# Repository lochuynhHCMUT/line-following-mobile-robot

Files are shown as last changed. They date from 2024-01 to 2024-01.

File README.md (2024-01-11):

# Line following mobile robot with color sensor
This repository contains all files and documents for the Line following mobile robot. The robot was constructed for the Mechatronics Design Project Course at Ho Chi Minh City University of Technology (HCMUT). Our team member includes:
- Huynh Ba Loc
- Phan Dang Khoi Nguyen
- Truong An Quoc
- Nguyen Hoang Minh

The sequence of operation is as follow:
1. Starts following the line until the loading zone, which is marked by a horizontal line.
2. Stops and waits for the package.
3. After the package is loaded, determines its color and chooses a corresponding path.
4. Follows the chosen path.
5. Stops at the end of the line.

The robot can be seen working in [this video](https://youtu.be/HqmgRXV4fzo?si=YYQn4gw1GglHw1m8).



## Building the robot
The robot is built by following [this assembly drawing](ME4071_Mechanical_Assembly_drawing_HuynhBaLoc_NguyenHoangMinh_PhanDangKhoiNguyen_TruongAnQuoc.pdf).

<!-- <img src="3d-robot.png"> -->

## PCB
All required PCBs are located in [this PCB folder](pcb).

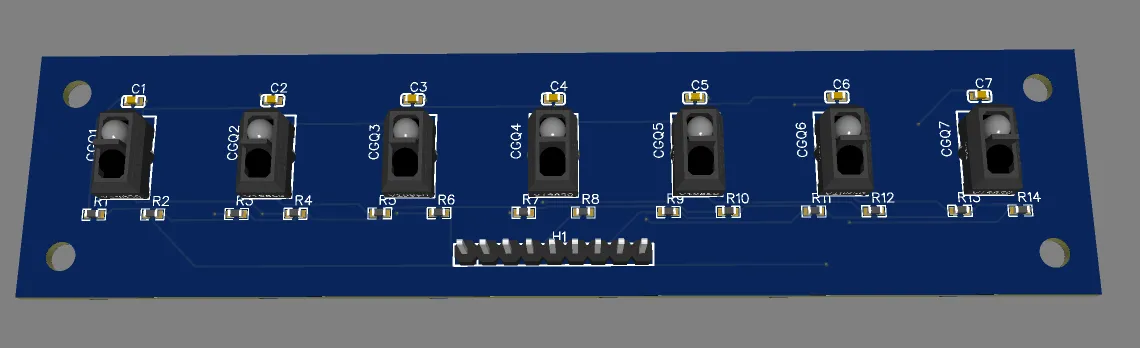
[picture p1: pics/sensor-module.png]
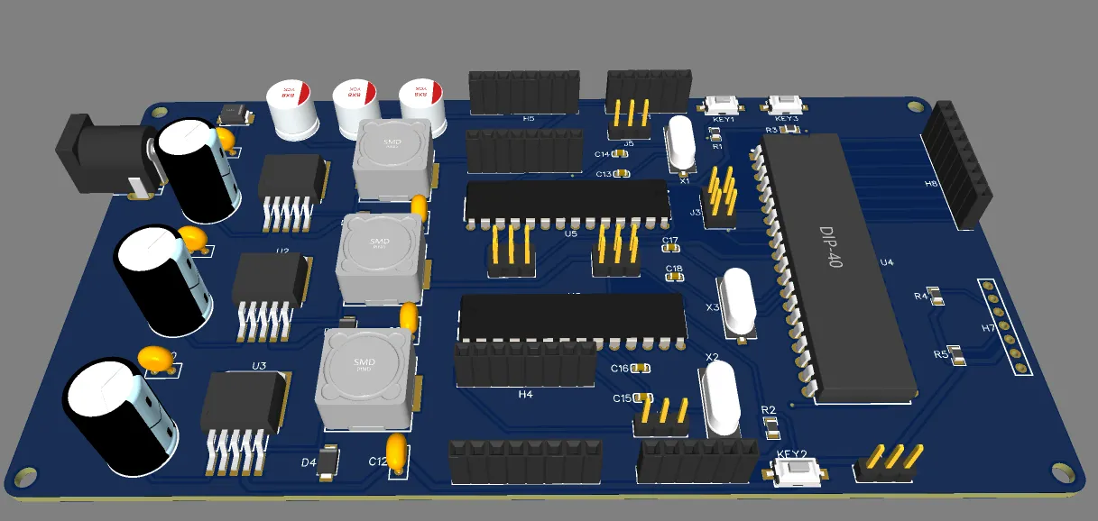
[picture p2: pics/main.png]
 

## Motor PID
To be updated.

## Sensor calibration
After constructing the robot, the line detecting sensor module needs to be calibrated. This MAX-MIN values of each sensor are obtained and set in [the main code](code/A32-MasterMCU.ino).

## Uploading the code
The codes are uploaded using [this AVR USBasp](https://hshop.vn/products/mach-nap-avr-usbasp-2) from Arduino IDE. 

## Notes
To be updated.

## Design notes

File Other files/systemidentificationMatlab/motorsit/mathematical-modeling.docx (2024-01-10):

## 1. Modeling of motor

### 1.1. Define parameters for motor sampling

Test with L298N motor driver

We examine the linear relation between the input (%PWM) and the output revolution of the motor’s shaft (rpm) . To do that, we PWM signal is fed into the motor, duty cycle from 5-100% . After that, we read the rpm signal from the encoder.

Table 4.1. Table of rpm data of motor

%PMW | rpm
5% | 0
10% | 0
15% | 28.133
20% | 50.7385
25% | 69.346
30% | 85.8935
35% | 104.143
40% | 118.375
45% | 129.678
50% | 141.245
55% | 151.046
60% | 161.361
65% | 168.31
70% | 176.172
75% | 181.71
80% | 187.617
85% | 192.982
90% | 198.063
95% | 202.461
100% | 219.046

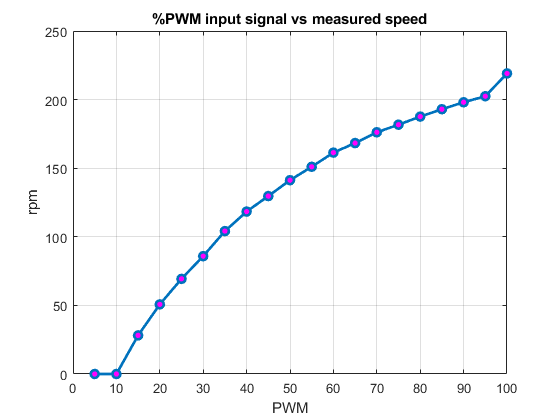
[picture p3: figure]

Fig 4.2. %PWM vs measured velocity (rpm) graph

Test with TB6612 motor driver

Follow the same procedure as above:

Table 4.2. Table of rpm data of motor

%PMW | rpm
5% | 0
10% | 21.4281
15% | 33.0784
20% | 45.6978
25% | 59.2714
30% | 71.612
35% | 85.1655
40% | 98.9197
45% | 111.3331
50% | 123.494
55% | 136.1053
60% | 149.1838
65% | 162.2477
70% | 176.4101
75% | 187.6647
80% | 198.401
85% | 214.4792
90% | 229.4622
95% | 241.7738
100% | 254.8411

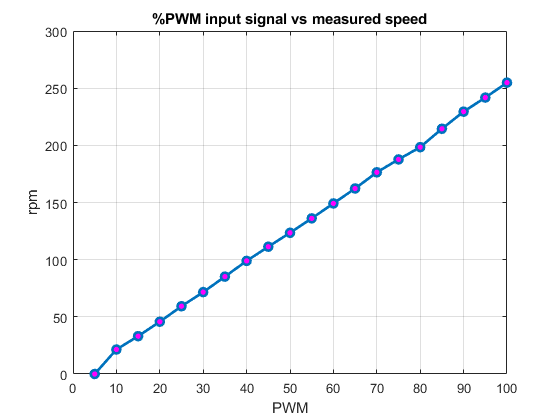
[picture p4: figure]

Fig 4.3. %PWM vs measured velocity (rpm) graph

We see that the TB6612 helps making the relationship between PWM and speed linear better than L298N.

### 1.2. Determine motor transfer function

Prepare data for SIT

Let a PWM input changes in the function f(t)=127.5sin(t)+127.5

→T=6.28(s)

Then:

N×δt=m×T

δt is from the Nyquist criterion

f_(Sampling) ≥2f_(signal) →δt≤1/2T

Our T satisfy the condition.

→N×0.022=m×6.2832

We choose N=1428; m=5 (must be integer)

For the motor, the output signal is the revolution of the output shaft (rpm) , input is PWM in a sinusoidal wave. So in order to obtain the motor transfer function, we will provide the motor with %PWM , then measure the revolution of the output shaft.

- Plotting the input and output data. We obtain the following graph:

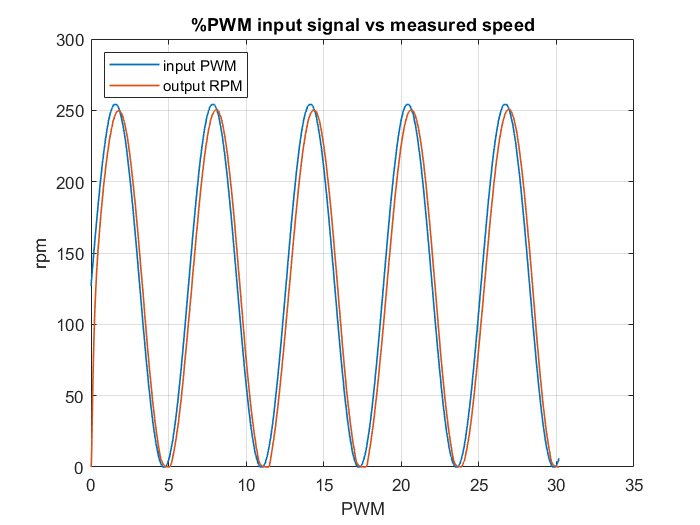
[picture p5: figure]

Fig 4.3. Measured speed of the motor

- Using MATLAB System Identification Toolbox (SIT), we yield the following transfer function of the motor-driver plant 1

G(s)=1.008/(0.18162×s+1)= 5.55/(s+5.51)

| Current value
Settling time | T_s =0.18162×4=0.72648 (s)
Overshoot | 1%
Steady-state error for step input | 0.01

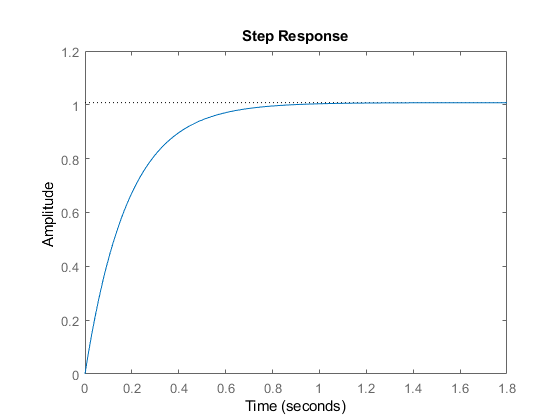
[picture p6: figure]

Fig 4.4. Step response graph of the transfer function

We want to make the motor-driver settling time smaller than the sampling time of the microcontroller so that it can work fine. T_s <δt

Select T_s =0.015 s

Keep the overshoot at this moment. We also want to remove steady-state error for step input

With the above requirements, we implement the PI controller for this motor-driver plant. Assuming negative unity feedback, the forward transfer function will be

K((s+a_2 ))/s×5.55/(s+5.51)

ζ=-(ln(%OS))/(√(ln(%OS)^2 +π^2))=-(ln(0.01))/(√(ln(0.01)^2 +π^2))=0.8261

T_s =0.015=(-ln(0.02√(1-ζ^2)))/(ζω_n)→ω_n =(-ln(0.02√(1-0.8261^2)))/(0.015×0.8261)=361.991

Then the PI controller:

(K(s+a_2 ))/s

Desired characteristics equation for negative unity feedback:

1+(K(s+a_2 ))/s5.55/(s+5.51)=0→s^2 +5.51s+5.55Ks+5.55Ka_2 =0→{, ω_n =√(5.55Ka_2)=361.991, ζ=(5.51+5.55K)/(2ω_n)=(5.51+5.55K)/(2×361.991)=0.8261→{, a_2 =(361.991^2)/(106.7696×5.55)=221.1336, K=106.7696

The open loop TF:

(106.7696(s+221.1336))/s×5.55/(s_0 +5.51)

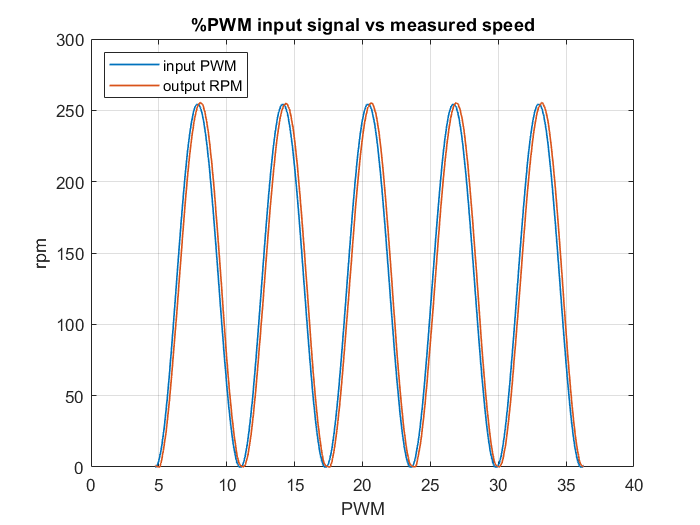
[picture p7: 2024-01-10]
Other files/systemidentificationMatlab/motorsit/motor2data.png

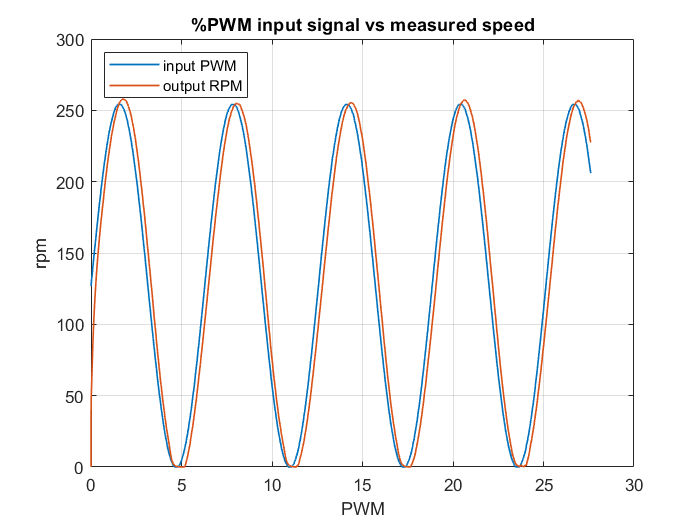
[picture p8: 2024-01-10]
Other files/systemidentificationMatlab/motorsit/checklinear(GM25+TB6612)/plotbytime.png

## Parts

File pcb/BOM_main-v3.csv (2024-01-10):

ID | Name | Designator | Footprint | Quantity
1 | 680uF | C1,C5,C9 | CAP-TH_BD10.0-P5.00-D1.0-FD | 3
2 | 100nF | C2,C4,C6,C8,C10,C12 | CAP-TH_L5.0-W2.5-P2.54-D0.7 | 6
3 | 220uF | C3,C7,C11 | CAP-TH_BD8.0-P3.50-D0.6-FD | 3
4 | 22p | C13,C14,C15,C16,C17,C18 | C0603 | 6
5 | SS34-SMB | D1,D5 | SMB_L4.4-W3.6-LS5.3-RD | 2
6 | IN5824 | D2,D3,D4 | SMAF_L3.5-W2.6-LS4.7-RD | 3
7 | DC005-2.0MM | DC1,DC2 | DC-IN-TH_DC005 | 2
8 | GM25 | H1,H2 | HDR-F-2.54_1X6 | 2
9 | TB6612 BLeft | H3 | HDR-F-2.54_1X8 | 1
10 | TB6612 BRight | H4 | HDR-F-2.54_1X8 | 1
11 | TB6612 ALeft | H5 | HDR-F-2.54_1X8 | 1
12 | TB6612 ARight | H6 | HDR-F-2.54_1X8 | 1
13 | TCS34725 | H7 | FEMALE-HEADER-1X7 | 1
14 | TCRT5000 MODULE | H8 | HDR-F-2.54_1X9 | 1
15 | ICSP_SlaveA | J1 | HDR-M-2.54_2X3 | 1
16 | ICSP_SlaveB | J2 | HDR-M-2.54_2X3 | 1
17 | ICSP_Master | J3 | HDR-M-2.54_2X3 | 1
18 | UART_Master | J4 | HDR-M-2.54_1X4 | 1
19 | UART_SlaveA | J5 | HDR-M-2.54_1X3 | 1
20 | UART_SlaveB | J6 | HDR-M-2.54_1X3 | 1
21 | K2-3.6×6.1_SMD | KEY1,KEY2,KEY3 | KEY-SMD_2P-L6.2-W3.6-LS8.0 | 3
22 | 33uH | L1,L2,L3 | IND-SMD_L12.3-W12.3 | 3
23 | 10k | R1,R2,R3 | R0805 | 3
24 | 1k | R4,R5 | R0805 | 2
25 | LM2596S-12 | U1 | TO-263-5_L10.1-W8.7-P1.70-LS15.2-BR | 1
26 | LM2596S-5 | U2 | TO-263-5_L10.1-W8.7-P1.70-LS15.2-BR | 1
27 | LM2596S-3.3 | U3 | TO-263-5_L10.1-W8.7-P1.70-LS15.2-BR | 1
28 | ATMEGA32A-PU_Master | U4 | DIP-40_L52.3-W13.9-P2.54-LS15.2-BL | 1
29 | ATMEGA328P-PU_SlaveA | U5 | DIP-28_L34.6-W7.3-P2.54-LS10.2-BL | 1
30 | ATMEGA328P-PU_SlaveB | U6 | DIP-28_L34.6-W7.3-P2.54-LS10.2-BL | 1
31 | 16MHz | X1,X2,X3 | CRYSTAL-SMD_L11.4-W4.5-LS12.5 | 3

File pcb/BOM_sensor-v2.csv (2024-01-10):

ID | Name | Designator | Footprint | Quantity
1 | 100nF | C1,C2,C3,C4,C5,C6,C7 | CAP-TH_L5.0-W2.5-P2.54-D0.7 | 7
2 | TCRT5000L | CGQ1,CGQ2,CGQ3,CGQ4,CGQ5,CGQ6,CGQ7 | OPTO-TH_TCRT5000L | 7
3 | HDR-M-2.54_1x9 | J1 | HDR-M-2.54_1X9 | 1
4 | 4k7 | R1,R3,R5,R7,R9,R11,R13 | R0603 | 7
5 | 220 | R2,R4,R6,R8,R10,R12,R14 | R0603 | 7

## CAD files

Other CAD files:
File CAD 2023/Assembly drawing.dwg
File CAD 2023/Selection and Algorithms.dwg
File CAD 2023/Electrical drawing.dwg

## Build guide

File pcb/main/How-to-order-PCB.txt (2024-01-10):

How to Order PCB

Please refer to:
https://docs.easyeda.com/en/PCB/Order-PCB

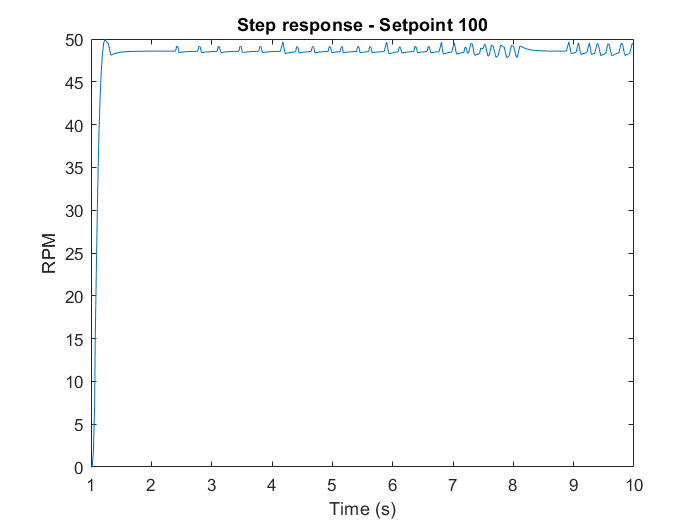
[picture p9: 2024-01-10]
Other files/systemidentificationMatlab/motorsit/step100.png

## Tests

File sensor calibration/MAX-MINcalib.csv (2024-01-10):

 | CB1 | CB2 | CB3 | CB4 | CB5 | CB6 | CB7
 | 467 | 48 | 48 | 39 | 39 | 37 | 39
 | 468 | 52 | 37 | 39 | 39 | 37 | 40
 | 468 | 45 | 37 | 39 | 40 | 32 | 26
 | 469 | 41 | 40 | 40 | 26 | 26 | 30
 | 468 | 45 | 37 | 39 | 39 | 33 | 40
 | 466 | 48 | 48 | 48 | 39 | 37 | 39
 | 450 | 34 | 34 | 38 | 48 | 48 | 39
 | 464 | 52 | 37 | 39 | 39 | 37 | 40
 | 465 | 41 | 40 | 26 | 26 | 30 | 35
 | 463 | 40 | 40 | 26 | 27 | 31 | 38
 | 464 | 48 | 48 | 39 | 39 | 37 | 39
 | 465 | 40 | 26 | 26 | 30 | 34 | 38
 | 451 | 26 | 27 | 34 | 38 | 48 | 48
 | 468 | 45 | 37 | 39 | 40 | 32 | 26
 | 458 | 39 | 48 | 48 | 48 | 37 | 39
 | 458 | 40 | 26 | 30 | 34 | 38 | 48
 | 468 | 45 | 41 | 40 | 26 | 26 | 30
 | 464 | 52 | 39 | 39 | 39 | 41 | 40
 | 458 | 42 | 48 | 48 | 39 | 37 | 39
 | 446 | 30 | 30 | 38 | 38 | 48 | 48
 | 456 | 40 | 26 | 30 | 34 | 38 | 48
 | 463 | 40 | 26 | 26 | 30 | 34 | 38
 | 464 | 52 | 39 | 39 | 39 | 37 | 40
 | 446 | 30 | 30 | 38 | 38 | 48 | 48
 | 446 | 30 | 31 | 38 | 38 | 48 | 48
 | 447 | 30 | 31 | 38 | 48 | 48 | 48
 | 468 | 45 | 39 | 40 | 40 | 26 | 27
 | 466 | 48 | 48 | 39 | 39 | 37 | 39
 | 466 | 45 | 39 | 39 | 39 | 33 | 40
 | 469 | 45 | 41 | 40 | 26 | 26 | 30
 | 463 | 40 | 26 | 30 | 34 | 35 | 48
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

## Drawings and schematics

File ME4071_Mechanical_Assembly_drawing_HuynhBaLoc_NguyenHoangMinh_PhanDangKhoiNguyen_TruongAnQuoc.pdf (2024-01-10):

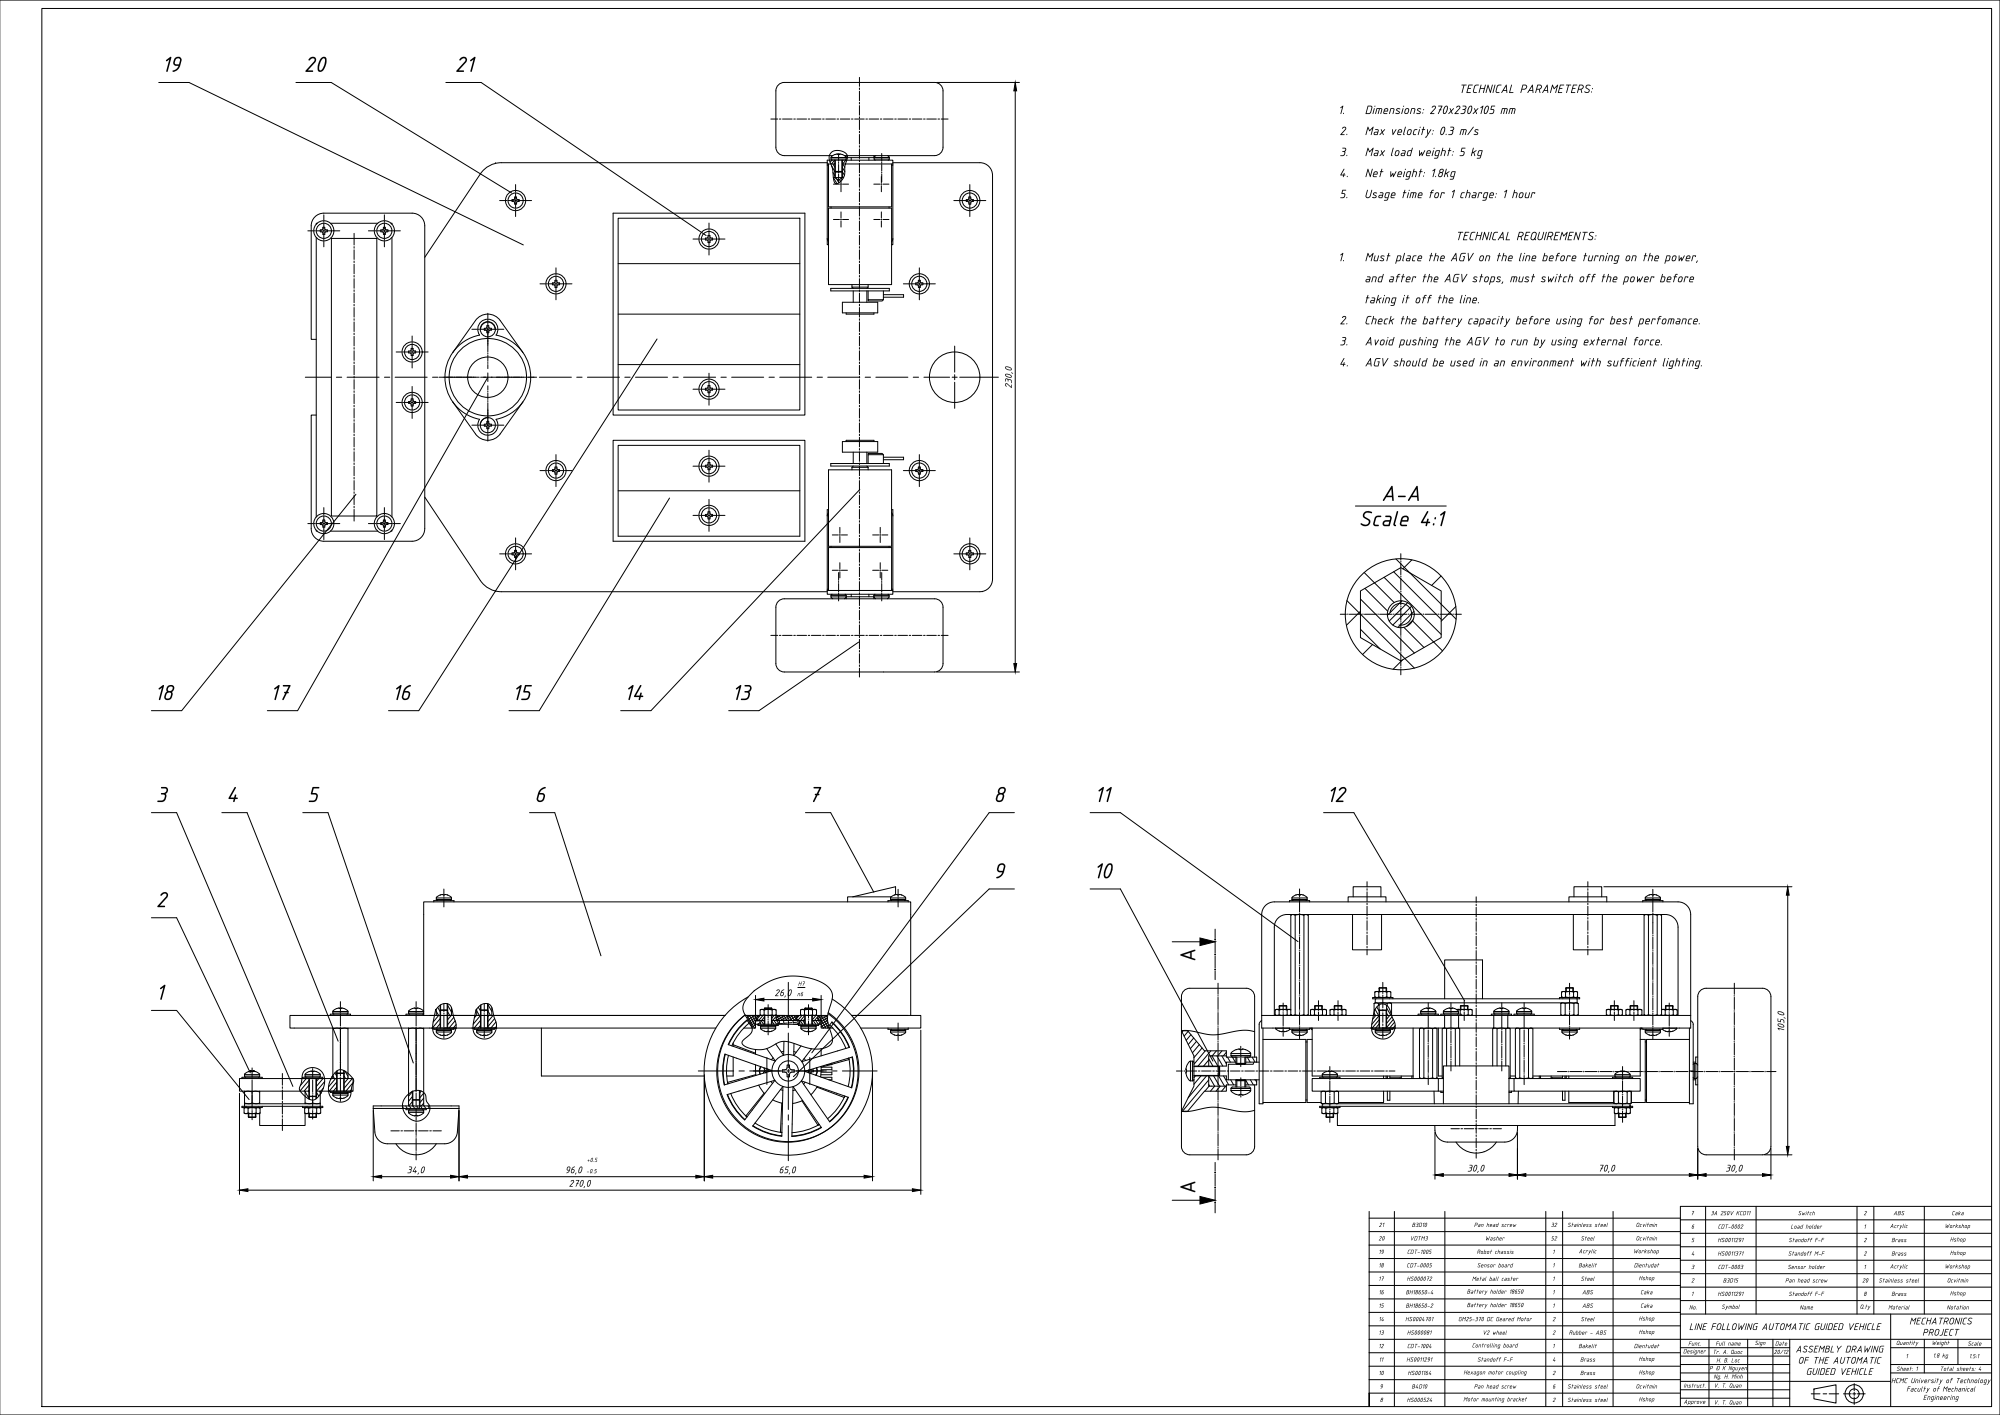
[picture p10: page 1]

230,0 Func. Full name Sign Date Quantity Weight Scale 1 Sheet: 1 Total sheets: 4 Designer Instruct. Approve Tr. A. Quoc V. T. Quan V. T. Quan 20/12 MECHATRONICS PROJECT ASSEMBLY DRAWING OF THE AUTOMATIC GUIDED VEHICLE LINE FOLLOWING AUTOMATIC GUIDED VEHICLE HCMC University of Technology Faculty of Mechanical Engineering 1.8 kg 1.5:1 H. B. Loc P Đ K Nguyen Ng. H. Minh No. Symbol Name Q.ty Material Notation 1 Standoff F-F 8 Brass 2 Pan head screw 20 Stainless steel 3 Sensor holder 1 Acrylic 4 Standoff M-F 2 Brass 5 HS0011291 HS0011371 HS0011291 Standoff F-F 2 Brass 6 Load holder 1 Acrylic 8 Motor mounting bracket 2 Stainless steel 10 Controlling board 1 Bakelit 11 V2 wheel 2 12 Battery holder 18650 1 ABS 131415 Metal ball caster 1 16 Sensor board 1 17 Steel HS000524 HS000081 Battery holder 18650 1 ABS HS0004701 GM25-370 DC Geared Motor 2 Bakelit HS000072 HS0011291 Standoff F-F 4 Brass 1819 Robot chassis 1 Acrylic HS001164 Hexagon motor coupling 2 Brass 20 Washer 52 Steel 9 Pan head screw 6 Stainless steel 21 Pan head screw 32 Stainless steel 7 3A 250V KCD11 Switch 2 A-A Scale 4:1 TECHNICAL PARAMETERS: 1. Dimensions: 270x230x105 mm 2. Max velocity: 0.3 m/s 3. Max load weight: 5 kg 4. Net weight: 1.8kg 5. Usage time for 1 charge: 1 hour TECHNICAL REQUIREMENTS: 1. Must place the AGV on the line before turning on the power, and after the AGV stops, must switch off the power before taking it off the line. 2. Check the battery capacity before using for best perfomance. 3. Avoid pushing the AGV to run by using external force. 4. AGV should be used in an environment with sufficient lighting. B3D15 CDT-0003 CDT-0002 CDT-1005 CDT-1004 CDT-0005 B4D10 VDTM3 B3D10 BH18650-2 BH18650-4 Steel Rubber - ABS ABS Hshop Hshop Hshop Hshop Hshop Hshop Hshop Hshop Hshop Ocvitmin Ocvitmin Ocvitmin Ocvitmin Workshop Workshop Workshop Caka Caka Caka Dientudat Dientudat 30,0 70,0 30,0 H7 26,0 n6

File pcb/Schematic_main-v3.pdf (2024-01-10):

# C18 ¹⁶MHz X³

# C16 ¹⁶MHz X²

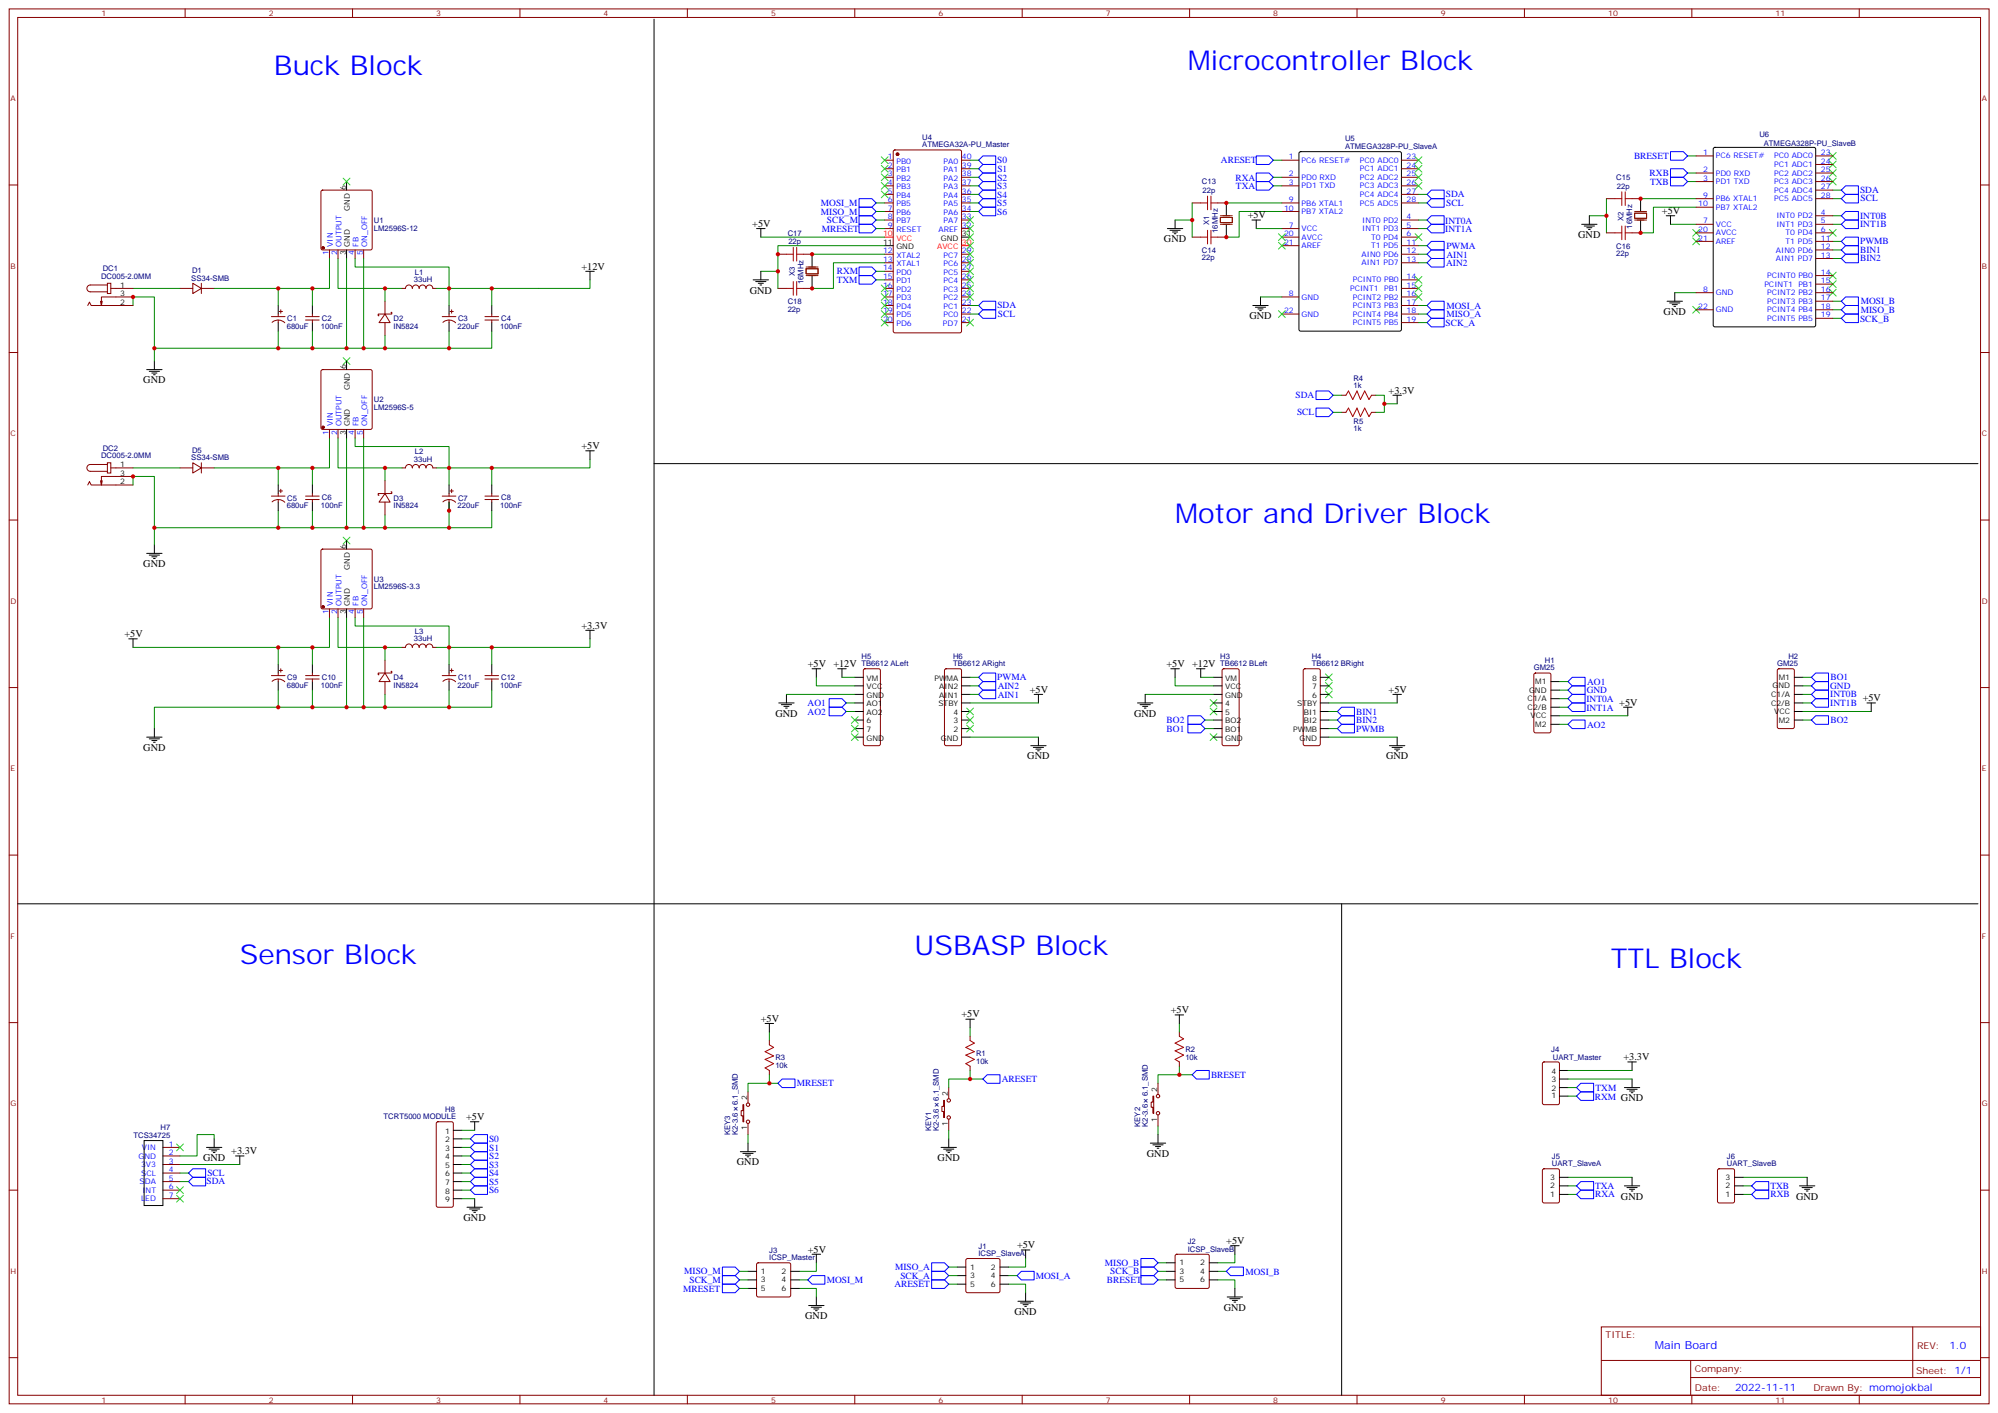
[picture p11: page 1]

Motor and Driver Block

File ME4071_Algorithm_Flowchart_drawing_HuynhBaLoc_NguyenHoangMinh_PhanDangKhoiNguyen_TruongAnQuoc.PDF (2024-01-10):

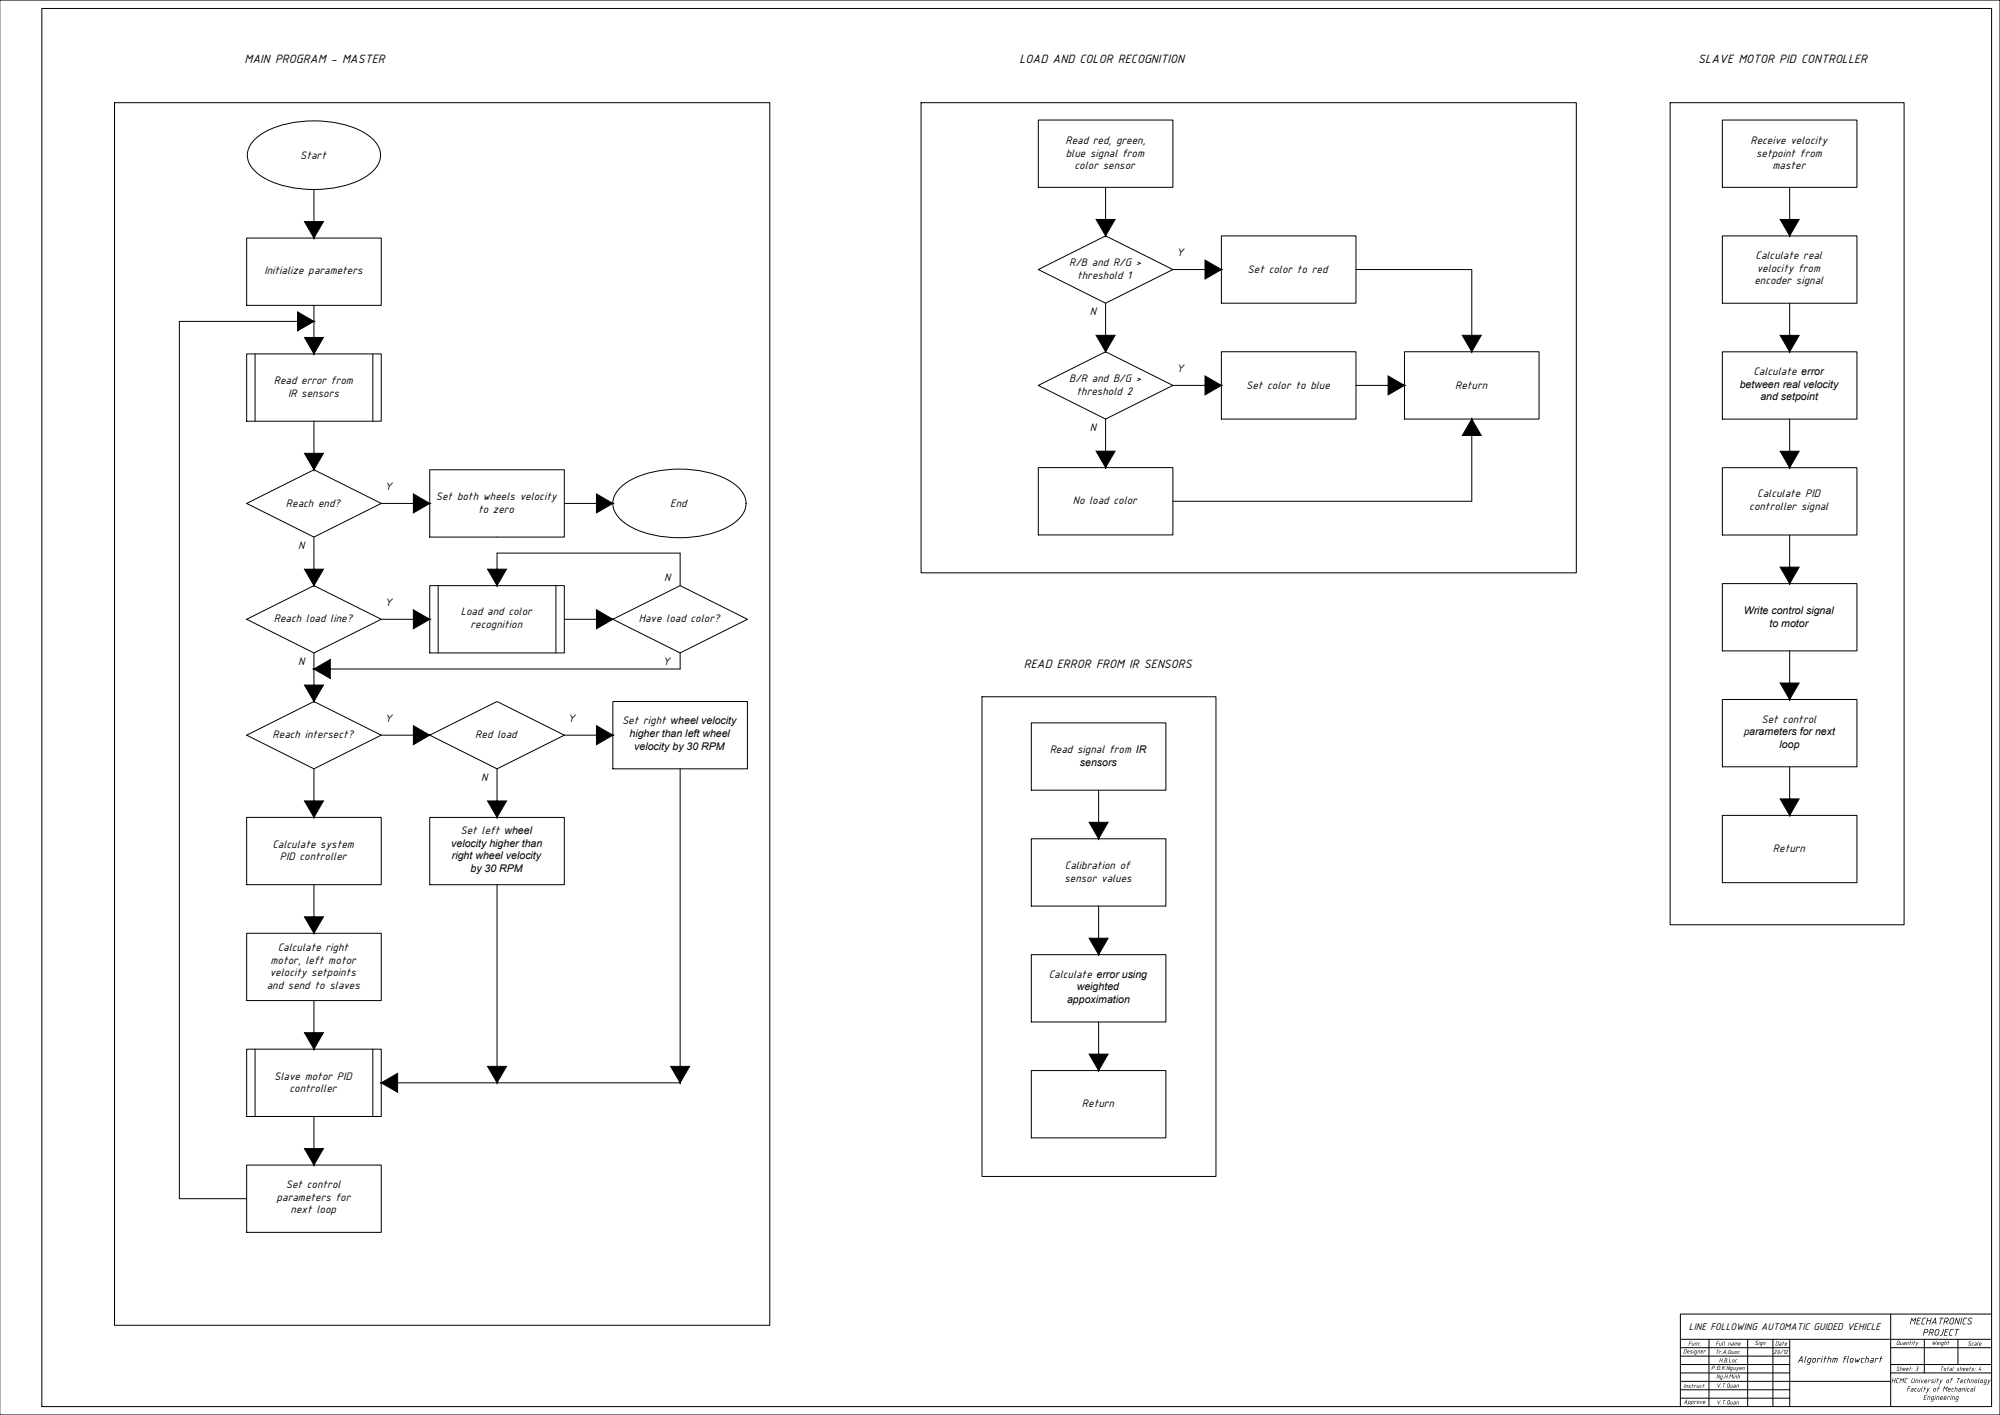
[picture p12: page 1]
MAIN PROGRAM - MASTER; LOAD AND COLOR RECOGNITION; SLAVE MOTOR PID CONTROLLER READ ERROR FROM IR SENSORS Start Initialize parameters Read error from IR sensors Reach end?; Set both wheels velocity to zero; End N Reach load line?; Load and color recognition N Reach intersect?; Red load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

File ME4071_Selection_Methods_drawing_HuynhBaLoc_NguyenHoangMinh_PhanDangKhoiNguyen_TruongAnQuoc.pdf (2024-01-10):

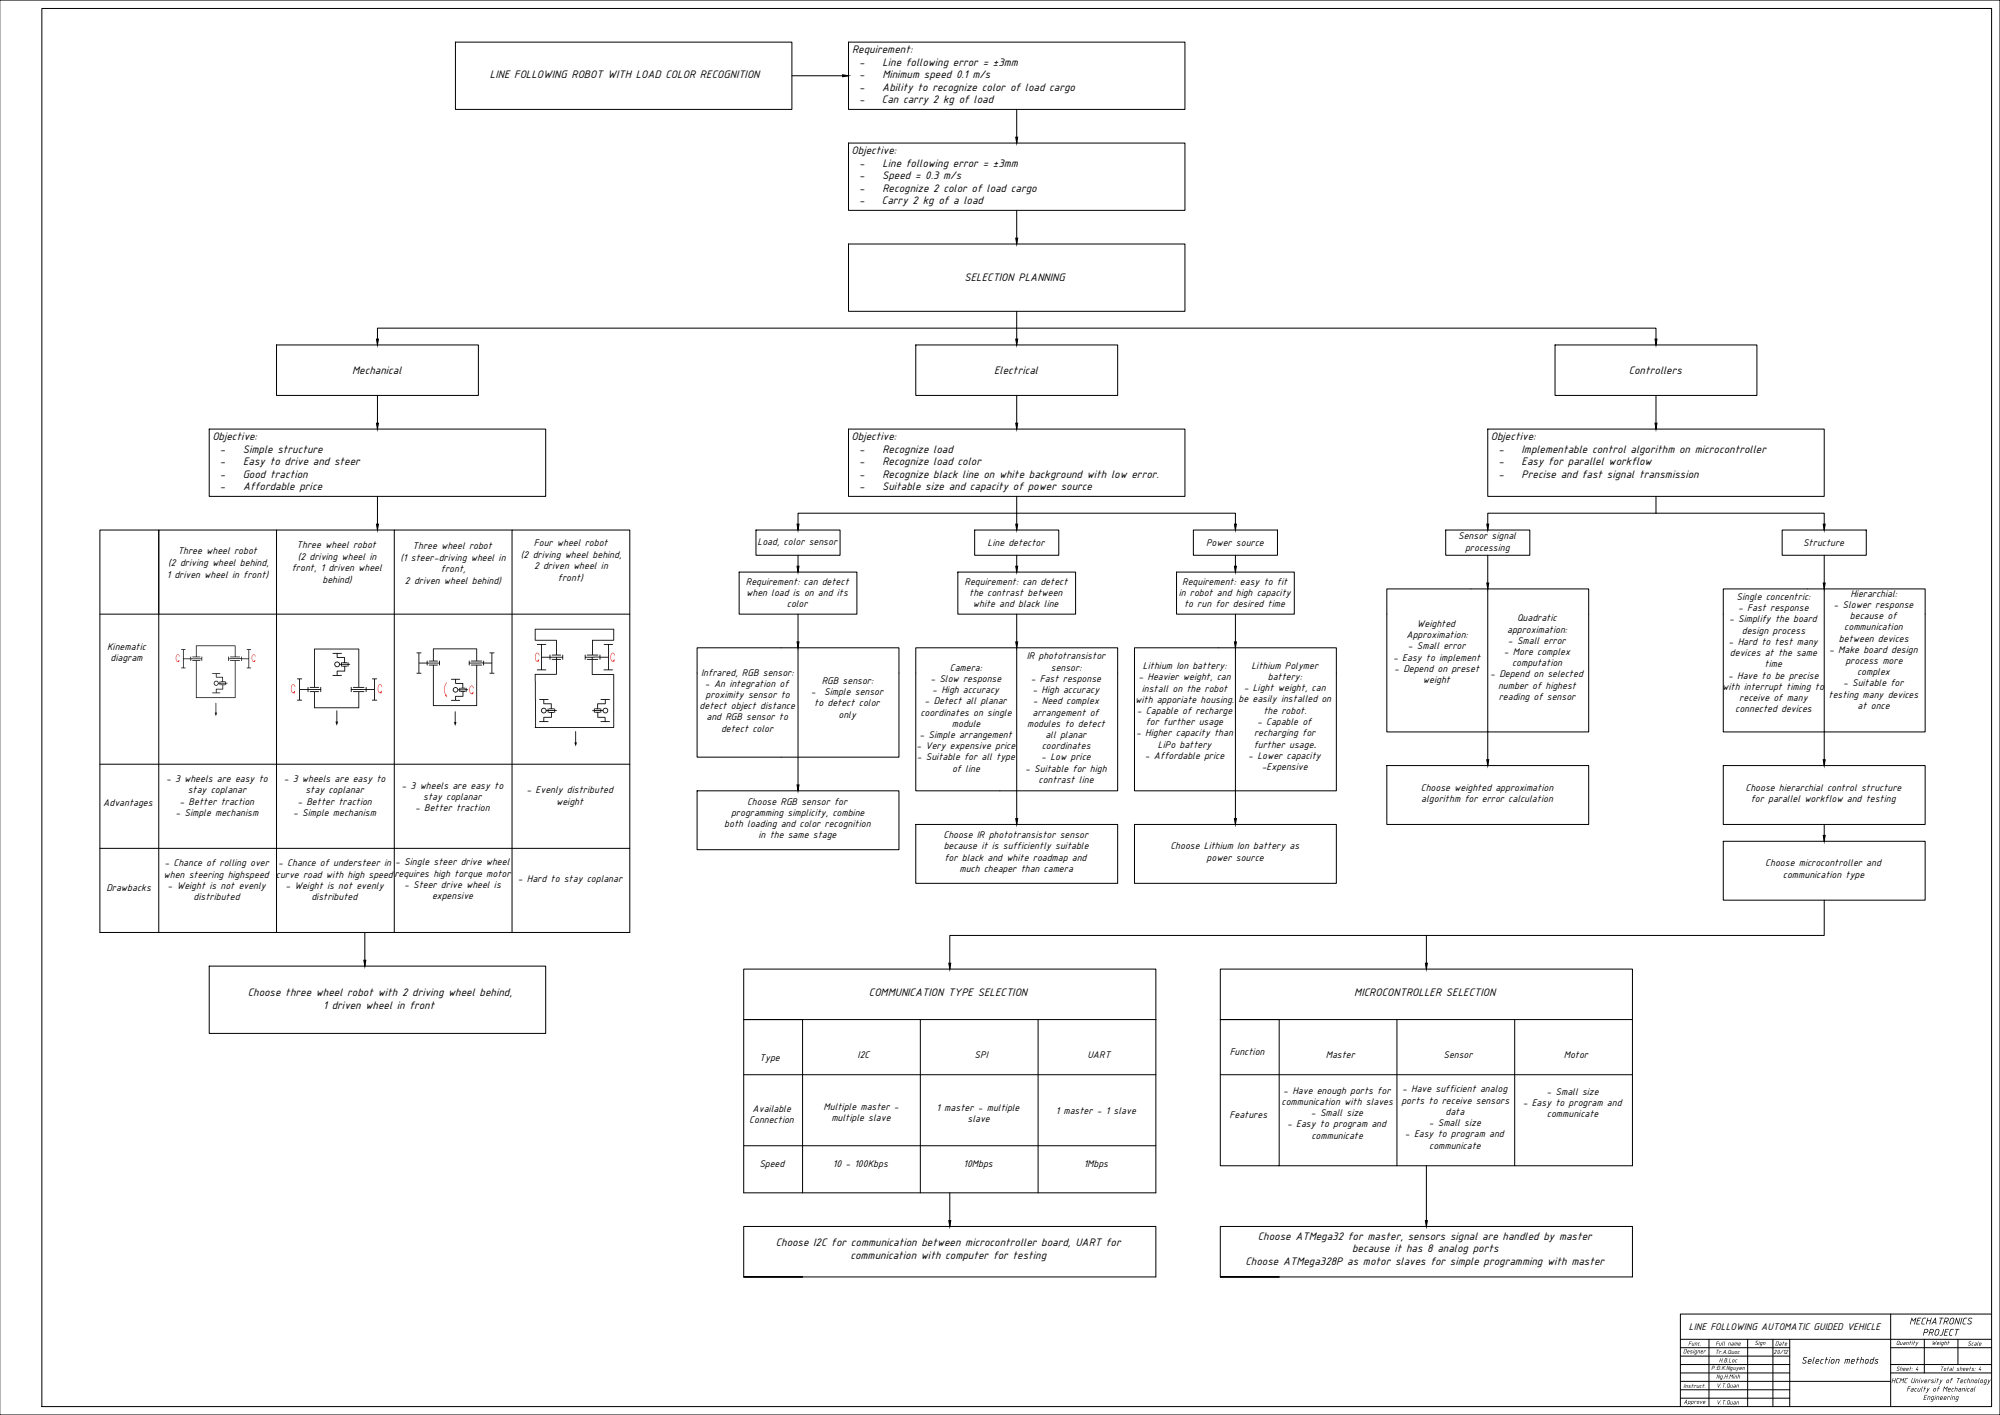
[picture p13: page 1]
Three wheel robot (2 driving wheel behind, 1 driven wheel in front); Three wheel robot (2 driving wheel in front, 1 driven wheel behind); Four wheel robot (2 driving wheel behind, 2 driven wheel in front) Three wheel robot (1 steer-driving wheel in front, 2 driven wheel behind); Load, color sensor; Line detector; Power source; Sensor signal processing; Structure Kinematic diagram Advantages Drawbacks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

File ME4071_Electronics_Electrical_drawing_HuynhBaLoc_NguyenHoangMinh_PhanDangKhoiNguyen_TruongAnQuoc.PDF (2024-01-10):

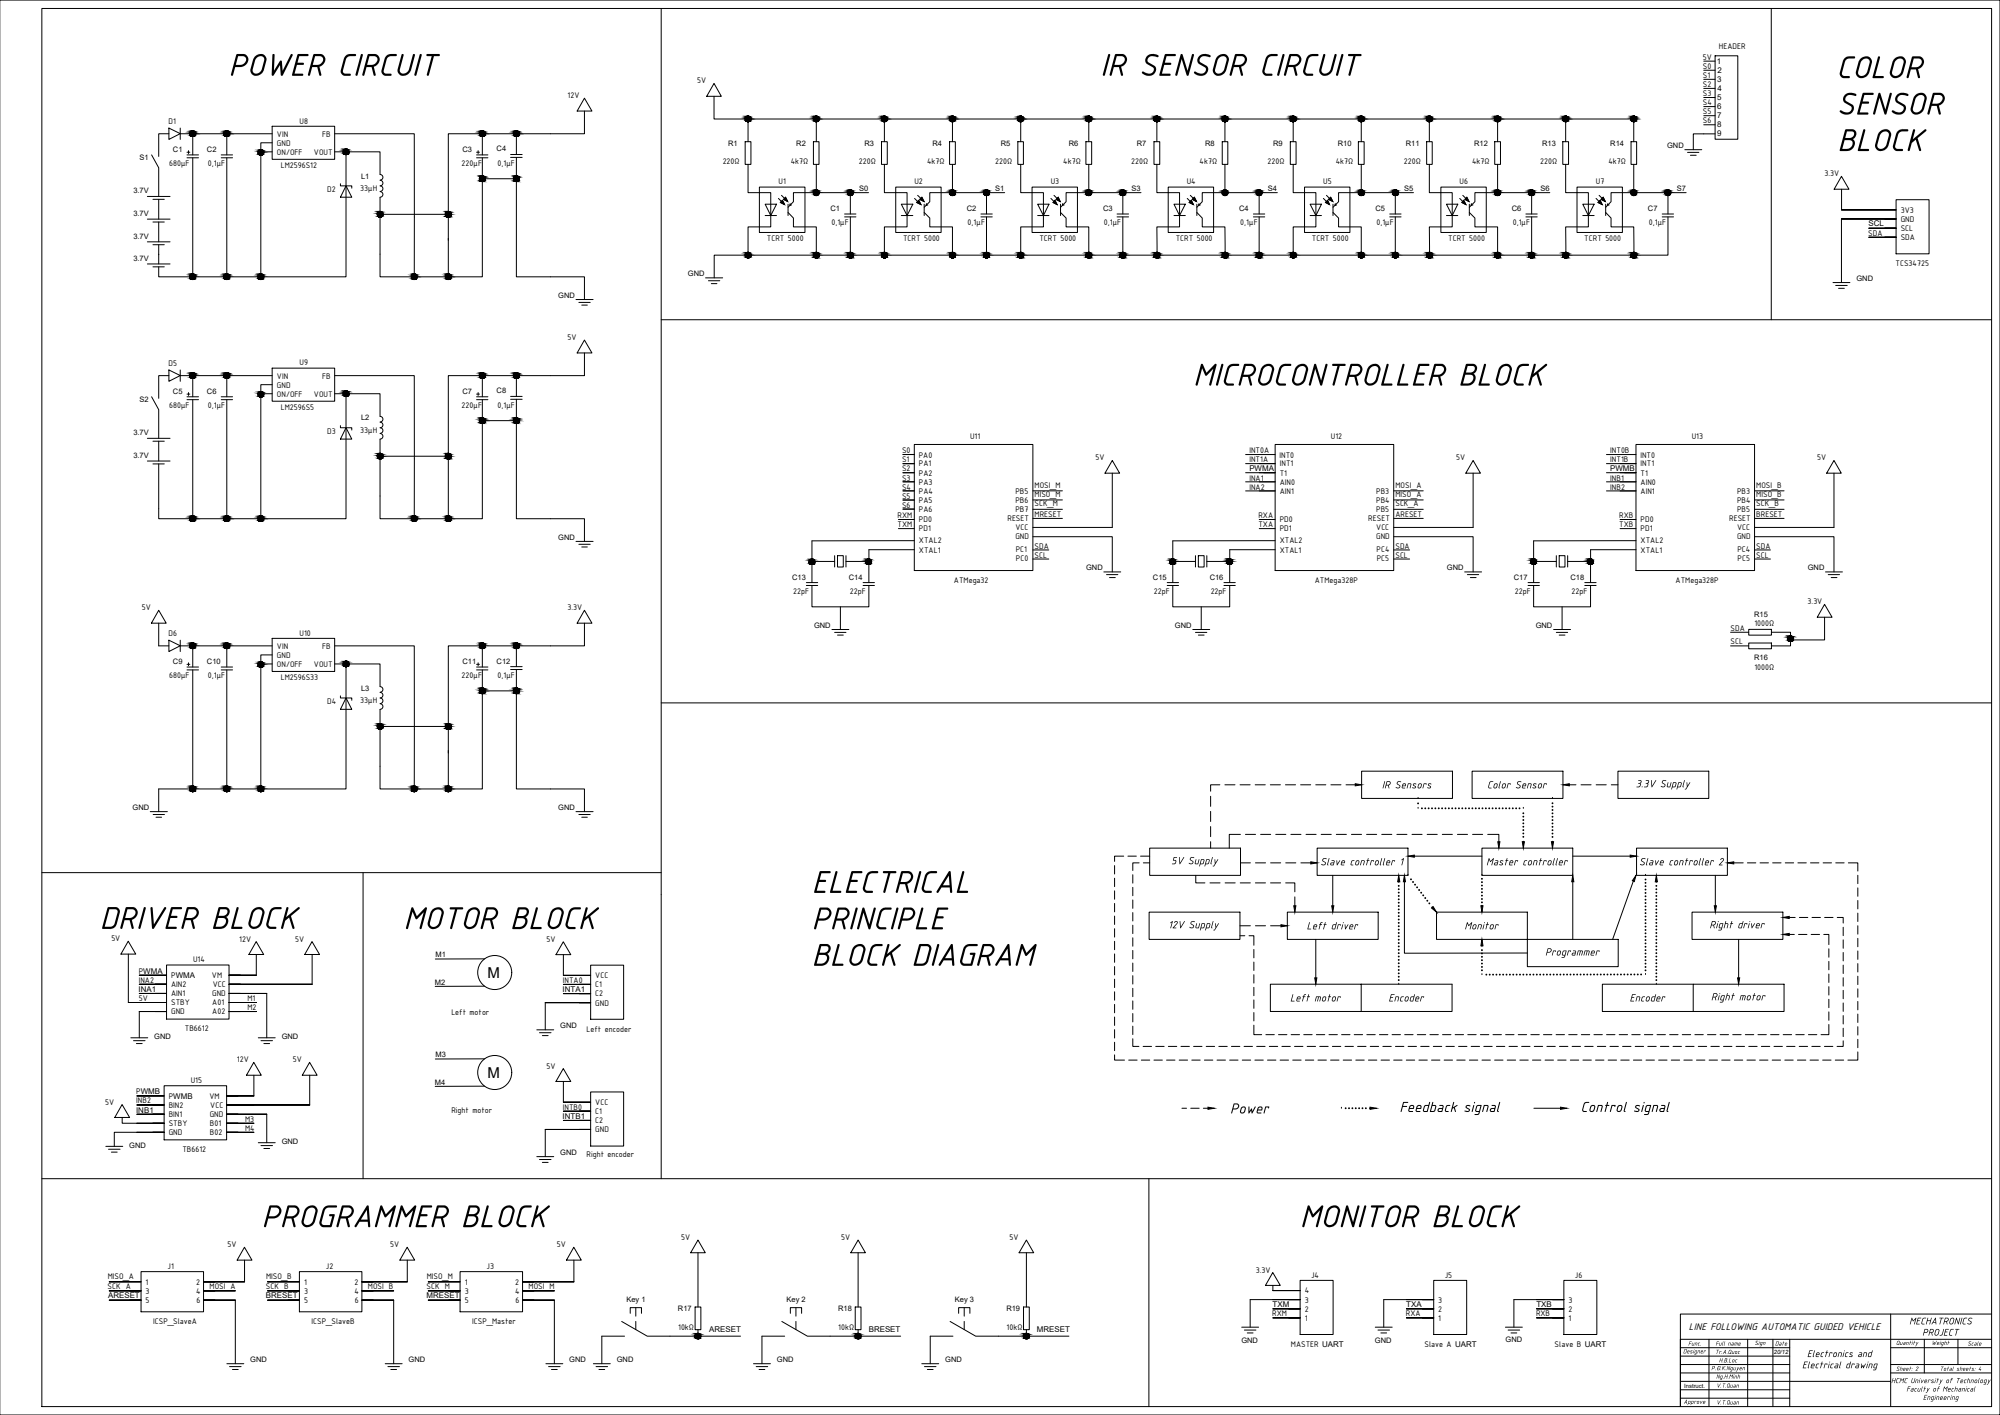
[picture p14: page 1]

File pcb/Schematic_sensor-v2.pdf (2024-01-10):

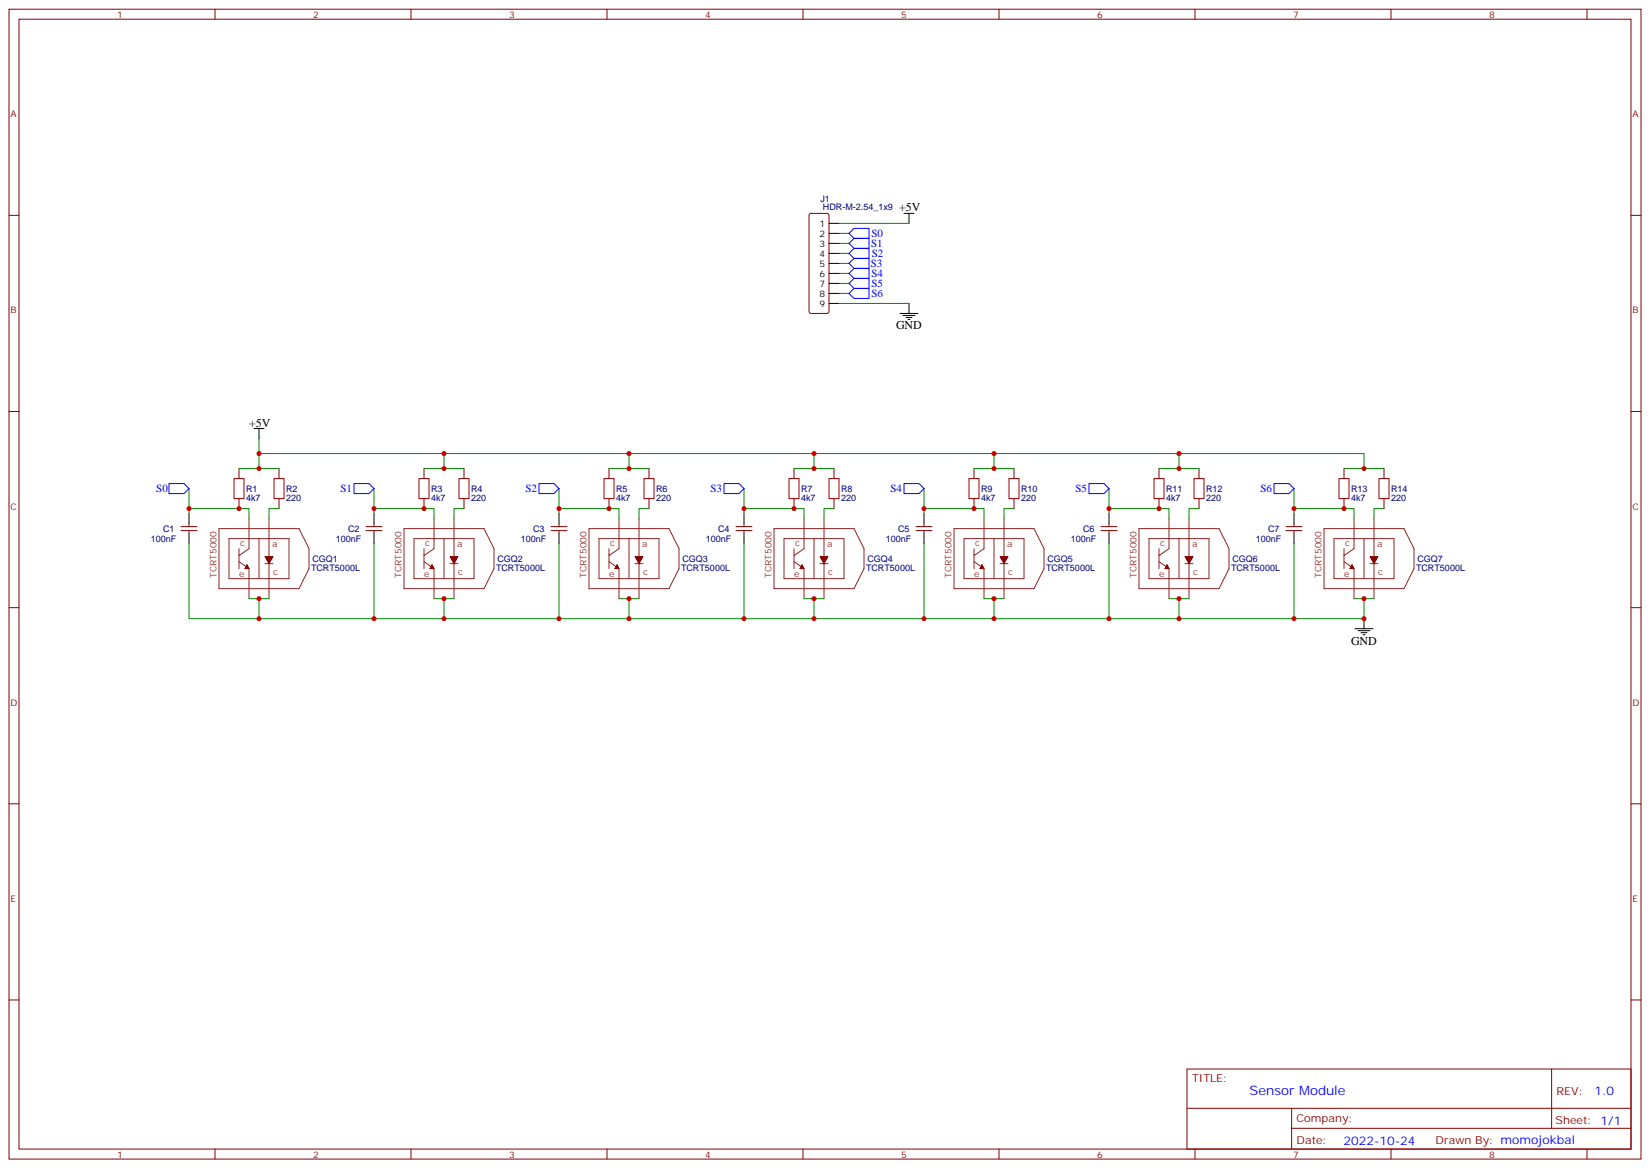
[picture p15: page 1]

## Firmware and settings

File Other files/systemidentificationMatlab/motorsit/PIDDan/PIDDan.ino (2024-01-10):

// Pins
#define ENCA 2
#define ENCB 3
#define PWM 5
#define IN1 7
#define IN2 6

// globals
long prevT = 0;
int posPrev = 0;
// Use the "volatile" directive for variables
// used in an interrupt
volatile int pos_i = 0;
volatile float velocity_i = 0;
volatile long prevT_i = 0;

float v1Filt = 0;
float v1Prev = 0;
float eprop =0, eder = 0, ePrev =0, ePast = 0;
float eintegral = 0;
float uPrev = 0;
int pwr = 120;
float vt = 120;
void setup() {
  Serial.begin(9600);
  pinMode(ENCA,INPUT);
  pinMode(ENCB,INPUT);
  pinMode(PWM,OUTPUT);
  pinMode(IN1,OUTPUT);
  pinMode(IN2,OUTPUT);
  attachInterrupt(digitalPinToInterrupt(ENCA),readEncoder,RISING);
}

void loop() {

  // read the position and velocity
  int pos = 0;

  noInterrupts(); // disable interrupts temporarily while reading
  pos = pos_i;

  interrupts(); // turn interrupts back on

  // Compute velocity with method 1
  long currT = micros();
  float deltaT = ((float) (currT-prevT))/1.0e6;
  float velocity1 = (pos - posPrev)/deltaT;
  posPrev = pos;
  prevT = currT;

  // Convert count/s to RPM
  float v1 = velocity1/374*60.0;

  // Low-pass filter (25 Hz cutoff)
  v1Filt = 0.854*v1Filt + 0.0728*v1 + 0.0728*v1Prev;
  v1Prev = v1;

  // Set a target


  // Compute the control signal uL
  float kp = 6.6;
  float ki = 75.55;
  float kd = 0.144144;
  float e = vt-v1Filt;
  //Proportional
   eprop = e - ePrev;
   // Integration 
  eintegral = e*deltaT;

  // Derivative 
  eder = (e - 2*ePrev + ePast)/deltaT;

  // PID calculations
  float u = uPrev + kp * eprop + ki * eintegral + kd * eder;

  // Set the motor speed and direction
  int dir = 1;
  if (u<0){
    dir = -1;
  }
  pwr = fabs(u);
  if(pwr > 255){
    pwr = 255;
  }
  setMotor(dir,pwr,PWM,IN1,IN2);
  uPrev = u;
  ePast = ePrev;
  ePrev = e;
  Serial.print(vt);
  Serial.print("\t");
  Serial.print(v1Filt);
  Serial.print("\t");
  Serial.print(currT/1e6);
  Serial.println();

}

void setMotor(int dir, int pwmVal, int pwm, int in1, int in2){
  analogWrite(pwm,pwmVal); // Motor speed
  if(dir == 1){ 
    // Turn one way
    digitalWrite(in1,HIGH);
    digitalWrite(in2,LOW);
  }
  else if(dir == -1){
    // Turn the other way
    digitalWrite(in1,LOW);
    digitalWrite(in2,HIGH);
  }
  else{
    // Or dont turn
    digitalWrite(in1,LOW);
    digitalWrite(in2,LOW);    
  }
}

void readEncoder(){
  // Read encoder B when ENCA rises
  int b = digitalRead(ENCB);
  int increment = 0;
  if(b>0){
    // If B is high, increment forward
    increment = 1;
  }
  else{
    // Otherwise, increment backward
    increment = -1;
  }
  pos_i = pos_i + increment;
  

}

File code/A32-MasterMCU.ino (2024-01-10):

#include <math.h>
#include <Wire.h>
#include <stdio.h>
#include "Adafruit_TCS34725_Hshopvn.h"

//I2C ADDRESS
#define address1 9 //SET SLAVE 1 I2C ADDRESS
#define address2 10 //SET SLAVE 2 I2C ADDRESS
//#define address3 0x29 (DEFAULT COLOR SENSOR I2C ADDRESS, CANNOT CHANGE)

//Declare variables
  //Color sensor reading
Adafruit_TCS34725_Hshopvn tcs = Adafruit_TCS34725_Hshopvn(TCS34725_INTEGRATIONTIME_700MS, TCS34725_GAIN_1X);  

  //IR Sensor reading
int s0 = 24;
int s1 = 25;
int s2 = 26;
int s3 = 27;
int s4 = 28;
int s5 = 29;
int s6 = 30;
int ss[7];
float calib_ss1 = 0;
float calib_ss2 = 0;
float calib_ss3 = 0;
float calib_ss4 = 0;
float calib_ss5 = 0;
float calib_ss6 = 0;
float calib_ss7 = 0;
float num = 0;
float den = 0;
float distss = 17;
int t_straight =0;

  //Load and Stop point parameters
int flag = 0;

 //Controller parameters
long prevT = 0;
float u = 0, q = 0;
float eprop =0, eder = 0, ePrev =0, ePast = 0;
float eintegral = 0;
float uPrev = 0;
int speed_left=0;
int speed_right =0;
int countstraight = 0;
int countcurve = 0;
float  dt = 0.26;
// CONFIG ORIGINAL
float Kp = 233;
float Ki = 11;
float Kd = 0.8;

int color = 0;

//Declare sub function

void read_sensor();
float weightedapprox_sensor();
void sendSpeed(int speedd, int address);
void stopcar();
void color_recognition();


void setup() {
  /// put your setup code here, to run once:
  Wire.begin(); // join I2C bus as the master
  ///Begining the serial
  Serial.begin(115200);
  delay(100);
}

void loop() {
  //long currT = micros();
  read_sensor();
  float e = weightedapprox_sensor()/1000.0;
if ((calib_ss1<70)&&(calib_ss2<70)&&(calib_ss3<70)&&(calib_ss4<70)&&(calib_ss5<70)&&(calib_ss6<70)&&(calib_ss7<70) && (flag ==3)){ 
  sendSpeed(0,address1);
  sendSpeed(0,address2); 
}

else {
    if ( loadline() && flag == 0 ){
    sendSpeed(0,address1);
    sendSpeed(0,address2);
    while (color == 0){
      color_recognition();
    }
      flag = 1;
      delay(2000);
      t_straight = millis()+1000;  
      Ki = 15;
      Kd = 1;

    }
//    else if ( loadline() && flag == 1 && (countstraight <120)){
//      while (flag == 1){
//        speed_left = 88;
//        speed_right = 88;
//        sendSpeed(speed_right,address2); 
//        sendSpeed(speed_left,address1);     
//        countstraight = countstraight + 1;
//        if (countstraight == 119){
//          flag = 2;
//          Serial.print(flag);
//              Serial.print("\t");   
//        }
//        
//      }
//    }
    else if (millis() > t_straight && flag == 1) 
          { flag = 2;}    
    else if ( loadline() && flag == 2 && color == 1 && (countcurve <800)){
      while (flag == 2){
        speed_left = 70;
        speed_right = 120;
        sendSpeed(speed_right,address2); 
        sendSpeed(speed_left,address1);     
        countcurve = countcurve + 1;
        if (countcurve == 799){
          flag = 3;
          Serial.print(flag);
              Serial.print("\t");   
        }
      }
    }
    else if  ( loadline() && flag == 2 && color == 2 && (countcurve <800)){
      while (flag == 2){
        speed_right = 70;
        speed_left = 10;
        sendSpeed(speed_right,address2); 
        sendSpeed(speed_left,address1);     
        countcurve = countcurve + 1;
        if (countcurve == 799){
          flag = 3;
          Serial.print(flag);
              Serial.print("\t");   
        }
      }
    }
       eprop = e - ePrev;
       eintegral = e*dt;
       eder = (e - 2*ePrev + ePast)/dt;
       
    u = uPrev + Kp * eprop + Ki * eintegral + Kd * eder;
    speed_right = 88 + u;
    speed_left = 88 - u;
  uPrev = u;
  ePast = ePrev;
  ePrev = e;
       sendSpeed(speed_right,address2); 
    sendSpeed(speed_left,address1);

}
 
    Serial.print(flag);
    Serial.print("\t");   
    Serial.print(e,4);
    Serial.print("\t");  
    Serial.print(color);
    Serial.print("\t");         
//    Serial.print(speed_left);
//     Serial.print("\t");       
//    Serial.print(speed_right);  
//    Serial.print("\t");   
   // Serial.print(currT/1e6);
    Serial.println("");  
}
    



/////////////////////////////////
bool loadline (){
  if ( (calib_ss3 > 350) && (calib_ss4 > 250) && (calib_ss5 > 250) || \
       (calib_ss2 > 350) && (calib_ss3 > 250) && (calib_ss4 > 250) || \
       (calib_ss4 > 350) && (calib_ss5 > 250) && (calib_ss6 > 250) || \
       (calib_ss1 > 350) && (calib_ss2 > 250) && (calib_ss3 > 250) || \
       (calib_ss5 > 350) && (calib_ss6 > 250) && (calib_ss7 > 250) ){
    return true;
  }
  return false;
}
void read_sensor(){
  ss[0] = analogRead(s0);
  ss[1] = analogRead(s1);
  ss[2] = analogRead(s2);
  ss[3] = analogRead(s3);
  ss[4] = analogRead(s4);
  ss[5] = analogRead(s5);
  ss[6] = analogRead(s6); 

}

float weightedapprox_sensor(){
   calib_ss1 = 26 +(423.0/528.0)*(ss[0]-26);
   calib_ss2 = 26 +(423.0/401.0)*(ss[1]-26);
   calib_ss3 = 26 +(423.0/390.0)*(ss[2]-26);
   calib_ss4 = 26 +(423.0/427.0)*(ss[3]-26);
   calib_ss5 = 26 +(423.0/444.0)*(ss[4]-26);
   calib_ss6 = 26 +(423.0/323.0)*(ss[5]-26);
   calib_ss7 = 26 +(423.0/447.0)*(ss[6]-26);
   num = 3*(calib_ss7-calib_ss1)+2*(calib_ss6-calib_ss2)+(calib_ss5-calib_ss3);
    den = calib_ss1+calib_ss2+calib_ss3+calib_ss4+calib_ss5+calib_ss6+calib_ss7;

  float w_approx = distss*num/den;
  float w_error = (w_approx -0.2915)/0.7198;
  return w_error;
}
void stopcar(){
  sendSpeed(0,address1);
  sendSpeed(0,address2);    
}
void color_recognition(){
  uint16_t r, g, b, c;
  tcs.getRawData(&r, &g, &b, &c); 
//  Serial.print("R: "); Serial.print(r, DEC); Serial.print(" ");
//  Serial.print("G: "); Serial.print(g, DEC); Serial.print(" ");
//  Serial.print("B: "); Serial.print(b, DEC); Serial.print(" "); 
//  Serial.println(" ");  
  float rb = float(r)/float(b);
float rg = float(r)/float(g);
float br = float(b)/float(r);
float bg = float(b)/float(g);
//  Serial.print(rb);
//  Serial.print("\t");
//  Serial.print(rg);
//  Serial.print("\t");
//    Serial.print(br);
//  Serial.print("\t");
//    Serial.print(bg);
//  Serial.print("\t");
// 
//  Serial.println(" "); 

 if ((rb > 1.23 ) && (rg > 1.25)) {
  color = 1; //red
 } 
 else if ((br > 1.4) && (bg > 1.08)) {
  color = 2; //blue
 }
 else color = 0;
}

void sendSpeed(int speedd, int address) {
  Wire.beginTransmission(address); // informs the bus that we will be sending data to slave device 8 (0x08)
	Wire.write(speedd);        // send value_pot
	Wire.endTransmission();       // informs the bus and the slave device that we have finished sending data
}

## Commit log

2024-01-10 Up lan 2 full
    Upload necessary file
    [10.csv, 100.csv, 15.csv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]
2024-01-10 Update file cad
    Update file cad
    [Assembly drawing.dwg, Electrical drawing.dwg, Selection and Algorithms.dwg]
